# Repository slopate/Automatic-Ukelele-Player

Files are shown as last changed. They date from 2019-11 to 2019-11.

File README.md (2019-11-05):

# Automatic-Ukelele-Player

For this project, we wanted to use motors to actuate a physical instrument. We saw many of examples of this with percussion instruments in class, but we wanted to try something a bit more ambitious and went with a stringed instrument. We settled on a Ukulele because of it's portability, and because its strings are relatively easy to manipulate. Originally, we thought we would change the pitch of the strings by adjust the tuning pegs, which would be clipped to Servo motors. However it quickly became apparent that this would not give us the level of control that we wanted, and so we decided to move a slider along the fretboard instead.

Our custom hardware can be broadly broken down into two parts; the sliding mechanism and the strumming mechanism, which are each contained in their own project box and connected via a PVC pipe. The sliding mechanism uses a DC motor, which is attached to a threaded rod via a 3D printed mold that fits the shaft of the DC motor. On the threaded rod, there is a single nut, which is attached by popsicle sticks to a plastic sliding mechanism which rests on the fretboard of the ukulele. When the threaded rod spins, it causes the stationary nut to move along the axis of the rod, thus causing the sliding mechanism to move upwards and downwards on the fretboard.

The strumming mechanism is controlled via a Servo motor. We attached a popsicle stick to the top of the servo motor, which has a guitar pick clipped to the end. This pick then strums across the ukulele strings (in either direction) when the Servo is activated.

These two parts are each contained and wired within their own project boxes. The DC motor is mounted on the inside of a project box attached under the ukulele, and extends under the fretboard to the neck of the instrument. It is then secured in place by another project box, whose only purpose is to hold the other end of the threaded rod. There is then a third project box attached to the front of the ukulele, is connected to the the under-mounted box via a PVC pipe. This front-mounted box contains the ESP32 and both ultrasonic sensors, and has holes drilled for power output, which is being supplied by a volt battery. The servo motor is glued to the top of the project box. 

The user controls the automatic player with two ultrasound sensors, which detects the distance at which the ultrasound waves are blocked. This allows the user to control the ukulele by moving their hands closer and further from the sensors. The sensor to the left of the ukulele controls the frequency of the strumming. The closer your move your hand to the sensor, the faster the strumming gets. The sensor to the right of the ukulele controls the speed and direction of the fretboard slider. At the closest hand position to the sensor, the slider moves down the fretboard at the highest speed. As you move your hand further away, the speed slows down, until you get to the midpoint at which the direction switches. 

We ran into a handful of issues while building the instrument. The primary one was figuring out how to attach the rather bulky threaded rod to a motor. We tried soldering and glueing, but ultimately both of these methods were too weak. We ended up 3D-printing a custom mold to attach the units together. Another issue was deciding which motor to use. Originally we were using a stepper motor, but this ended up being way too slow at moving the fretboard. We then switched to a DC motor, which was much faster. Another issue was applying an appropriate amount of pressure to the frets. Too much pressure and it would stifle the sound of the ukulele, but too little and the slider would fall over. To fix this, we used modeling clay, placed below the neck of the ukulele, which allowed to adjust the height of the instrument and thus effect how much pressure was being applied by the slider. 

Parts List:  
Ukulele  
3 Project Boxes  
LKY61 Servo Motor  
L298N DC Motor  
2 HC-SR04 Ultrasonic Sensors 
ESP32  
Threaded Rod and Nut  
PVC Pipe  
Protoboard and Wires  
Modeling Clay  
Plastic Tubing (used for slider)  
Popsicle sticks   
Guitar Pick (made from credit card)  
9 Volt Battery  
3D printed mold  

## Some Photos
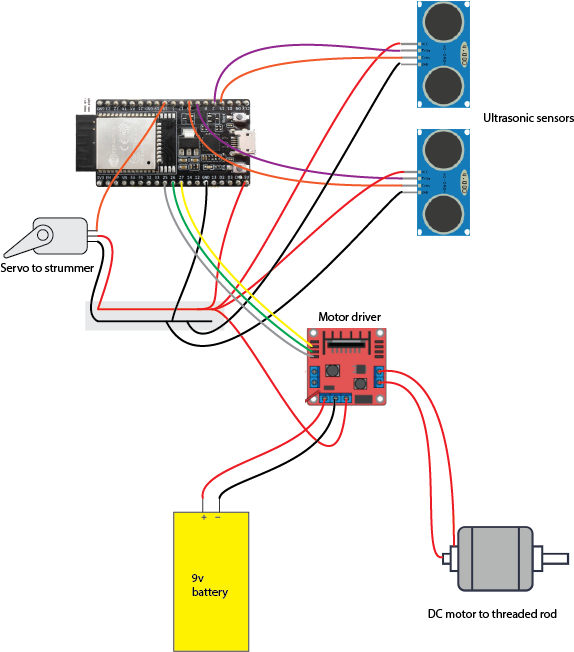
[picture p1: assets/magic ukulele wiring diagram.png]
Wiring


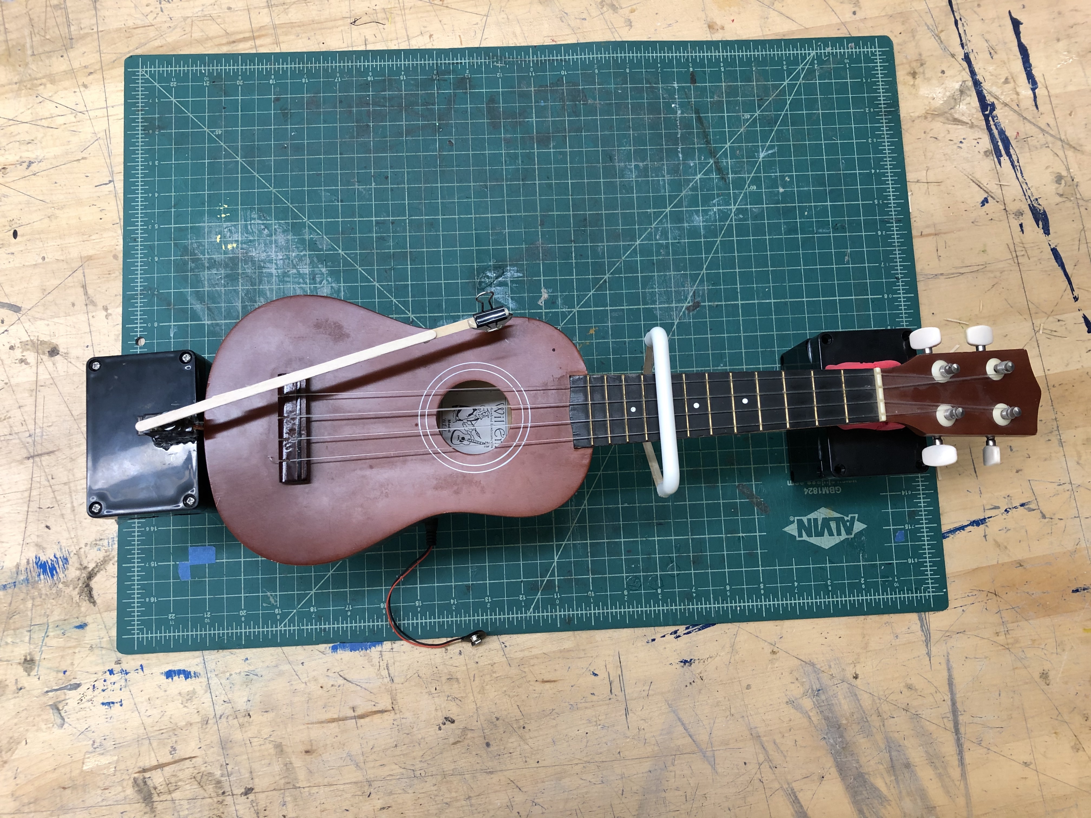
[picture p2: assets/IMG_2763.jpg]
Top down


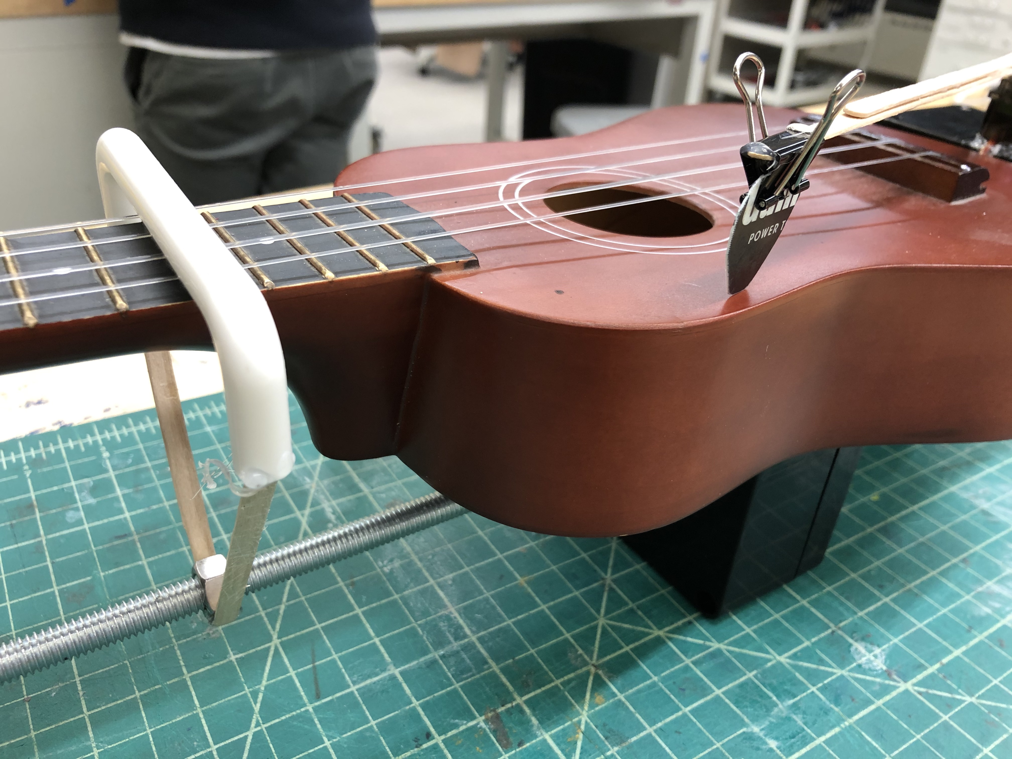
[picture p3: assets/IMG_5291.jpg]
Side


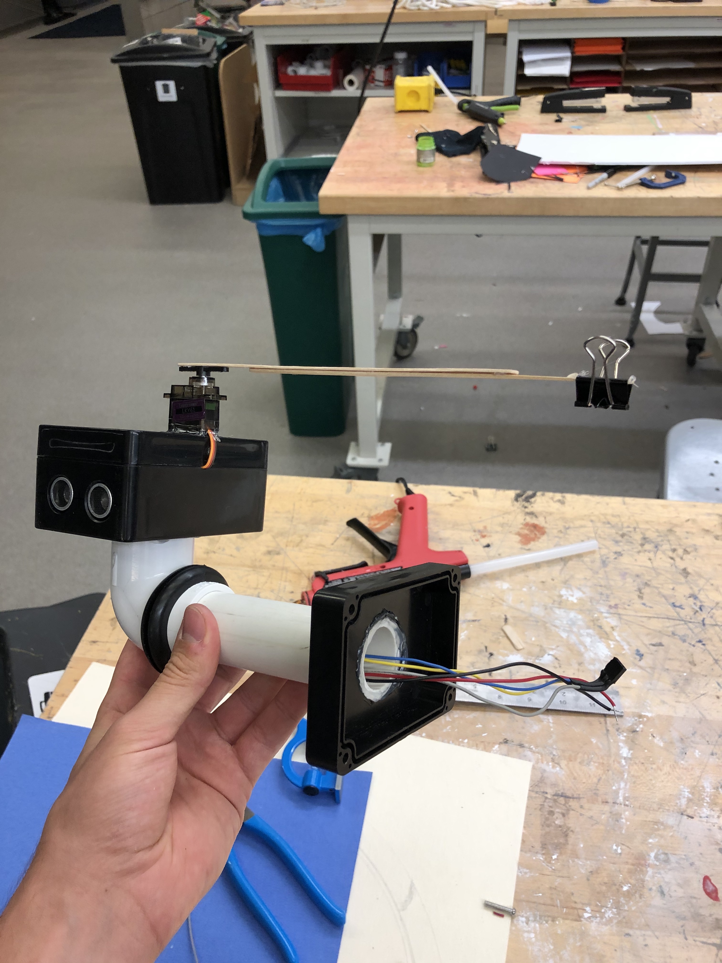
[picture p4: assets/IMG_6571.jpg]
Sensor assembly


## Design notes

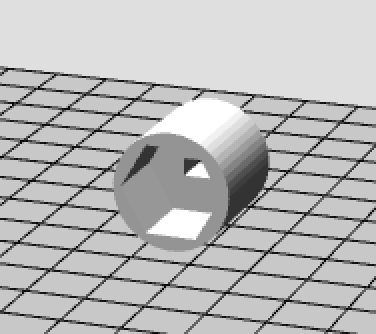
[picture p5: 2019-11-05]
stepper_threaded.png

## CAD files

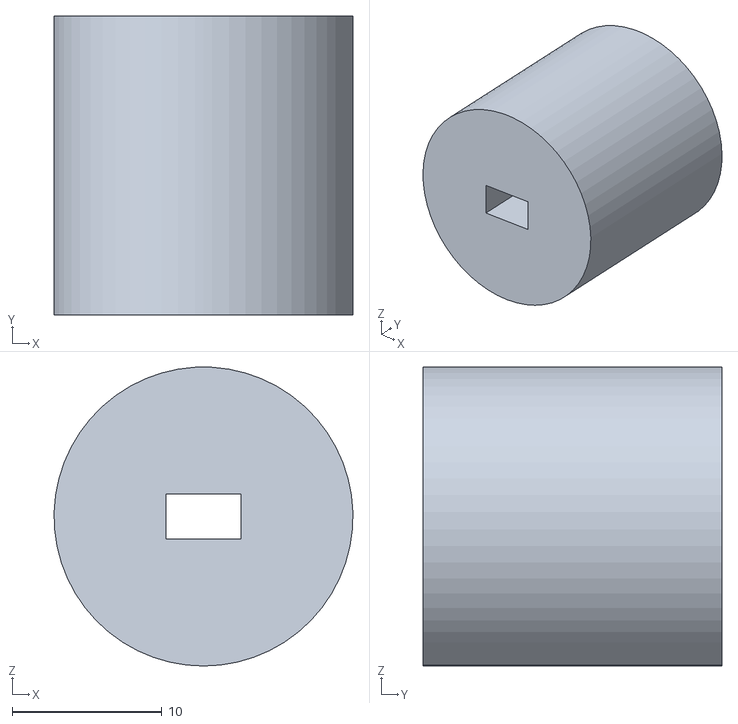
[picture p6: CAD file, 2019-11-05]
stepper_threaded.STL
20.0 x 20.0 x 20.0

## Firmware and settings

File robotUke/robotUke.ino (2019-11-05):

#include <ESP32Servo.h>
#include <analogWrite.h>

Servo myServo;

// variable declarations
int servoPos = 10;
int flag = 1;

long duration1;
long duration2;
long cm = 21.5;
long inches = 8.46;
long prevTime = 0;
int dcSpeed = 0;

// pin declarations
int trig1Pin = 16;
int echo1Pin = 4;
int trig2Pin = 2;
int echo2Pin = 15;

int dcSpeedPin = 25;
int dcDir1Pin = 26;
int dcDir2Pin = 27;

int servoPin = 18;


void setup() {
  //  set up serial, dc, and ultrasound pins
  Serial.begin(115200);
  myServo.attach(servoPin);

  pinMode(dcDir1Pin, OUTPUT);
  pinMode(dcDir2Pin, OUTPUT);

  pinMode(trig1Pin, OUTPUT);
  pinMode(echo1Pin, INPUT);
  pinMode(trig2Pin, OUTPUT);
  pinMode(echo2Pin, INPUT);

}

// method for reading from sonar sensor
int SonarSensor(int trigPin,int echoPin) {
  digitalWrite(trigPin, LOW);
  delayMicroseconds(2);
  digitalWrite(trigPin, HIGH);
  delayMicroseconds(10);
  digitalWrite(trigPin, LOW);
  return pulseIn(echoPin, HIGH);
}

void loop() {

  //  read sonar sensors
  duration1 = SonarSensor(trig1Pin, echo1Pin);
  duration2 = SonarSensor(trig2Pin, echo2Pin);

  //  print values
  Serial.print(duration1);
  Serial.print(',');
  Serial.println(duration2);

  // Convert the time into a distance
  if (duration1 < 10000) {
    cm = (duration1/2) / 29.1;     // Divide by 29.1 or multiply by 0.0343
    inches = (duration1/2) / 74;   // Divide by 74 or multiply by 0.0135
  }

  //  process data and move servo
  int delta = map(cm, 2, 30, 300, 3000);
  long curTime = millis();
  if (curTime - prevTime >= delta) {
    prevTime = curTime;

    myServo.write(servoPos);
    servoPos = servoPos + (30 * flag);
    flag = flag * -1;
  }

  //  handle DC motor direction and speed
  if (duration2 < 6300) {

    if (duration2 < 1000 ) {

      // set speed     
      dcSpeed = map(duration2, 0, 1000, 255, 0);
      analogWrite(dcSpeedPin, dcSpeed);
      
      // set direction
      digitalWrite(dcDir1Pin, LOW);
      digitalWrite(dcDir2Pin, HIGH);
    } else {

      // set speed     
      dcSpeed = map(duration2, 1000, 3000, 0, 255);
      analogWrite(dcSpeedPin, dcSpeed);

      // set direction
      digitalWrite(dcDir1Pin, HIGH);
      digitalWrite(dcDir2Pin, LOW);  
    }
    
  }

}

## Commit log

2019-11-03 main arduino code
2019-11-03 working w/ sensors, servo, and DC
2019-11-05 3D printer files
    [stepper_threaded.STL]
2019-11-05 wiring diagram
